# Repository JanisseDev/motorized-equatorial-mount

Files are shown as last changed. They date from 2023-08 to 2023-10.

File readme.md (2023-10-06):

# DIY Motorized Equatorial Mount

This project will guide you to create your own DIY Motorized Equatorial Mount controlled over wifi.

We will use a `28BYJ-48 stepper motor` coupled with a `1:42` reduction gear ratio, controlled by a `Raspberry Pico W`.
It'll be powered by `4xAA 1.2v Ni-MH rechargeable battery`.
> [!WARNING]
>_Do **not** use other battery than Ni-MH, since their voltage can be higher and damage your `Raspberry Pico W`._

<p align="center">
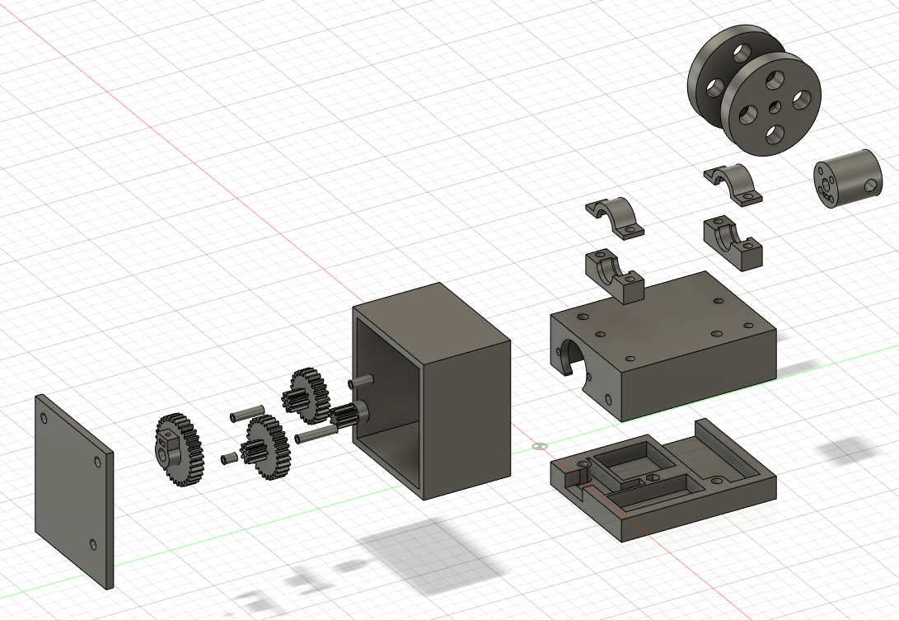
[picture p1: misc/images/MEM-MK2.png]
  
&nbsp;
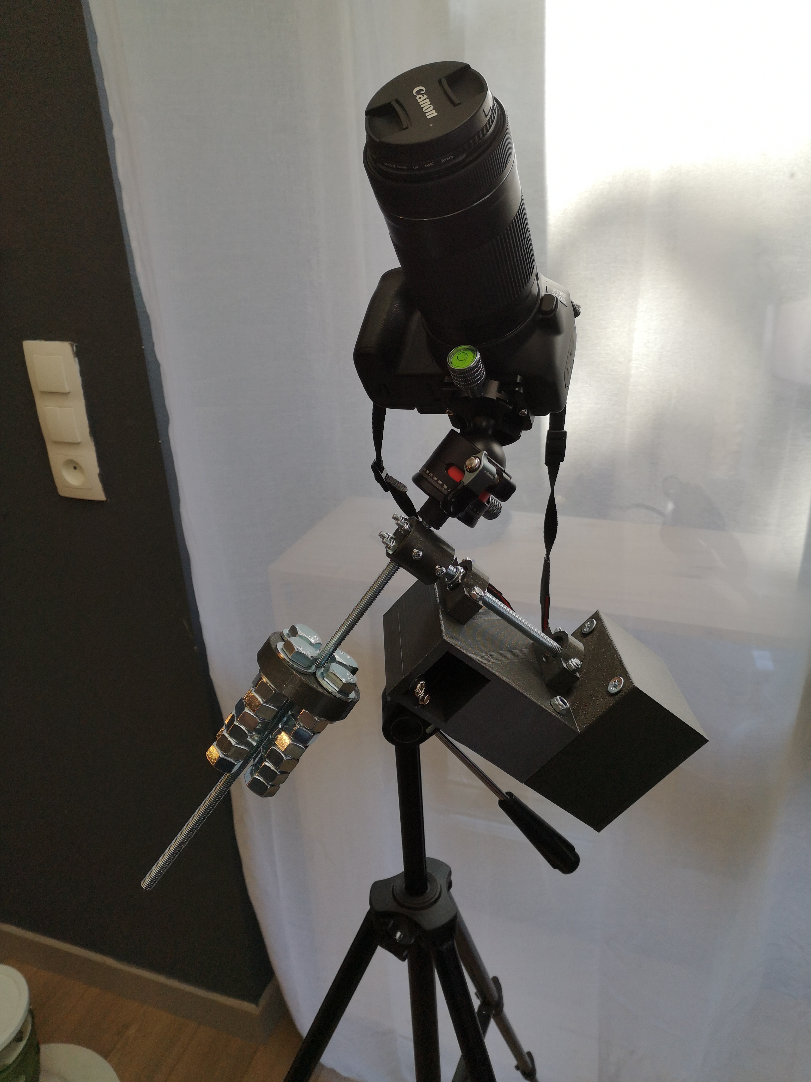
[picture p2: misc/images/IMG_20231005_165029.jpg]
  
</p>

## Item list
| Electronics | Case | Axis | Counterweight | Bearings |
| :---: | :---: | :---: | :---: | :---: |
| x1 Raspberry Pico W | x1 M6 bolt (80mm) | x1 M8 threaded Rod (500mm) | x1 M8 nut | x4 M5 bolt (30mm) |
| x1 28BYJ-48 stepper motor | x2 M6 bolt (70mm) | x2 M8 self-locking nut | x4 M12 screw (80mm) | x2 Skate bearing ABEC 7 |
| x1 ULN2003 driver board | x2 M6 bolt (50mm) | x4 M4 bolt (40mm) | x24 M12 nut | - |
| x1 4xAA case | x2 M4 bolt (20mm) | x2 M3 bolt (20mm) | - | - |
| Jumper wires | x1 M4 screw (40mm) | x1 M3 bolt (16mm) | - | - |
| - | x1 M4 wing nut | x2 nail (70mm x 3mm diameter) | - | - |

> [!NOTE]
>_This build requires some additional tools:_
> - _A metal saw to cut the M8 threaded Rod_
> - _A soldering iron to connect the power source to the Raspberry Pico W and the Motor driver board_

## Printing instructions
Print all the 3D files located in the [3dPrints](./misc/3dPrints/) folder.
All the files are already correctly oriented for printing, and are designed to use the smallest amount of supports as possible.
I printed these with an Ender-3 Pro, 0.4mm nozzle, layer height 0.2mm and with gyroid infill set to around 20% to 40%.
Some files needs to be printed multiple time, here is a list of pieces you should end up with:
| Count | Piece | Infill | Need supports |
| :---: | :---: | :---: | :---: |
| 1 | AxisMount-MEM-MK2 | 30% | Yes |
| 2 | BearingBottom-MEM-MK2 | 40% | No |
| 2 | BearingTop-MEM-MK2 | 40% | Yes |
| 2 | Counterweight-MEM-MK2 | 20% | No |
| 1 | Gear8-24-MEM-MK2 | 40% | No |
| 1 | Gear8-28-MEM-MK2 | 40% | No |
| 1 | Gear8-MEM-MK2 | 40% | No |
| 1 | Gear32-MEM-MK2 | 40% | No |
| 1 | GearSpacer8mm-MEM-MK2 | 40% | No |
| 1 | GearSpacer14mm-MEM-MK2 | 40% | No |
| 1 | GearSpacer20mm-MEM-MK2 | 40% | No |
| 1 | GearSpacer26mm-MEM-MK2 | 40% | No |
| 1 | GearCaseBottom-MEM-MK2 | 20% | No |
| 1 | GearCaseTop-MEM-MK2 | 20% | No |
| 1 | MainCaseBottom-MEM-MK2 | 20% | No |
| 1 | MainCaseTop-MEM-MK2 | 20% | Yes |

## Electrical diagram
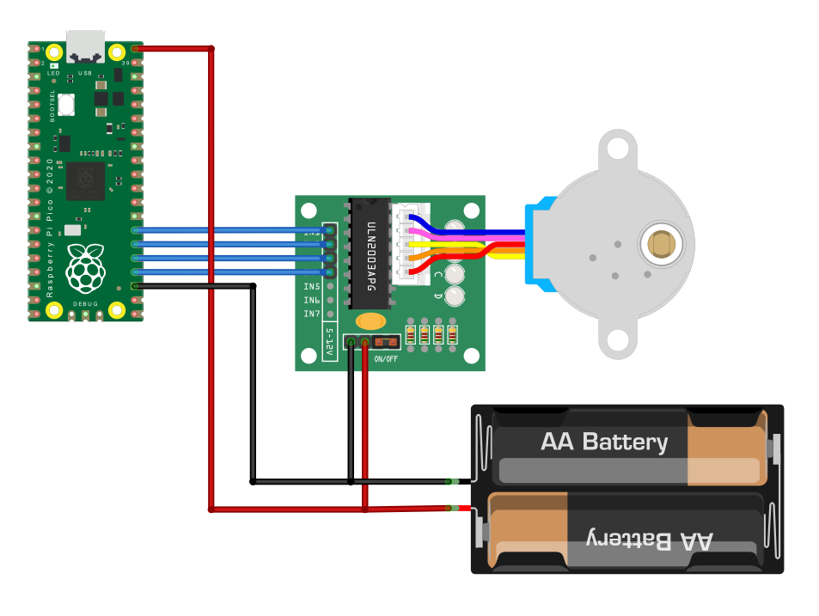
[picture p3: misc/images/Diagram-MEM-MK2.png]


## Assembly instructions
- Place the `Skate bearings` between `BearingTop` & `BearingBottom` pieces. Then mount them on the `MainCaseTop` with `x4 M5 bolt (30mm)`.
- Assemble the `Gear8` and the `motor` together.
- Place the `motor` inside the `GearCaseBottom`, put the `GearCaseBottom` on the side of `MainCaseTop` and screw them together with `x2 M4 bolt (20mm)`.
- Cut a 200mm piece from the `M8 threaded Rod`. We'll refer to it as the `main axis`. (Tip: You can easily cut a screw/rod without damaging it: screw some nuts near the spot you want to cut, clamp these nuts to a steady surface and cut your screw/rod)
- Put the `Gear32` at the very end of the `main axis` and secure it with a `x1 M3 bolt (16mm)`.
- Slide the `main axis` inside the bearings with the gear nearly inside the `GearCaseBottom` top. Secure it with `x2 M8 self-locking nut` by tightening the two nuts with a bearing between. (See [Gallery](#Gallery))
- Cut both ends of the `x2 nail (3mm diameter)` to a height of 60mm. These will serve as our intermediate gears' axes.
- Mount the `GearSpacer14mm`-`Gear8-24`-`GearSpacer20mm` on one of these axis, and put it inside the `GearCaseBottom`, in the furthest notch from the motor. (Tip: You can put some Blu-Tack inside the notch to help the axis standing while you assemble the whole thing)
- Repeat the process with the `GearSpacer26mm`-`Gear8-28`-`GearSpacer8mm`, in the nearest notch from the motor this time.
- Put the `GearCaseTop` on the `GearCaseBottom`, then secure it with `x2 M6 bolt (70mm)` and `x1 M6 bolt (80mm)`. (Make sure both intermediate gears axis are secured in their respective notch)
- Add `x4 M4 bolt (40mm)` to the `AxisMount`. (These are only here to secure the camera if the piece break)
- Mount the `AxisMount` on the `main axis` and secure it with `x1 M3 bolt (20mm)`.
- Cut a 300mm piece from the `M8 threaded Rod`. We'll refer to it as the `secondary axis`. (This axis will handle the camera and the counterweight)
- Mount the `secondary axis` on the `AxisMount` and secure it with `x1 M3 bolt (20mm)`.
- Put the `Raspberry Pico W` and the `ULN2003 driver board` inside the `MainCaseBottom`.
- Add `x1 M4 screw (40mm)` in the center hole. This will be used as a mounting screw on a tripod with the `x1 M4 wing nut`.
- Flash the `Raspberry Pico W` with [this binary](./misc/release/motorized_equatorial_mount.uf2).
- Connect all the electronics together (See the [electrical diagram](#electrical-diagram) above).
- Assemble the `MainCaseBottom` to the `MainCaseTop` with `x2 M6 bolt (50mm)`. (I highly suggest you to wrap the `4xAA case` wires around the screw)
- Put `x1 M8 nut` between the two `Counterweight` pieces and screw them together with `x4 M12 screw (80mm)` and `x24 M12 nut`. (You can put more or less nuts to customize your counterweight)
- You can now mount your camera on the `secondary axis` with an M8 to 1/4" adapter, for exemple, and screw the counterweight on the other side to balance it.

## User instructions
- Plug your 4xAA to the Motorized Equatorial Mount.
- Connect your phone to the wifi access point named `equatorial mount` (by default the password is `polar-star`). Open your browser and go to `192.168.4.1`
- You can now control the motor direction & speed from the web page. **The preset speed of 501ms between each motor step should be good to track stars if you use the same gear ratio & motor as mentioned in the Item list.**
- Unplug your 4xAA batteries to power down the system.
- Remove your camera and counterweight when not in use to prevent stress on the gears.

## Gallery
<p align="center">
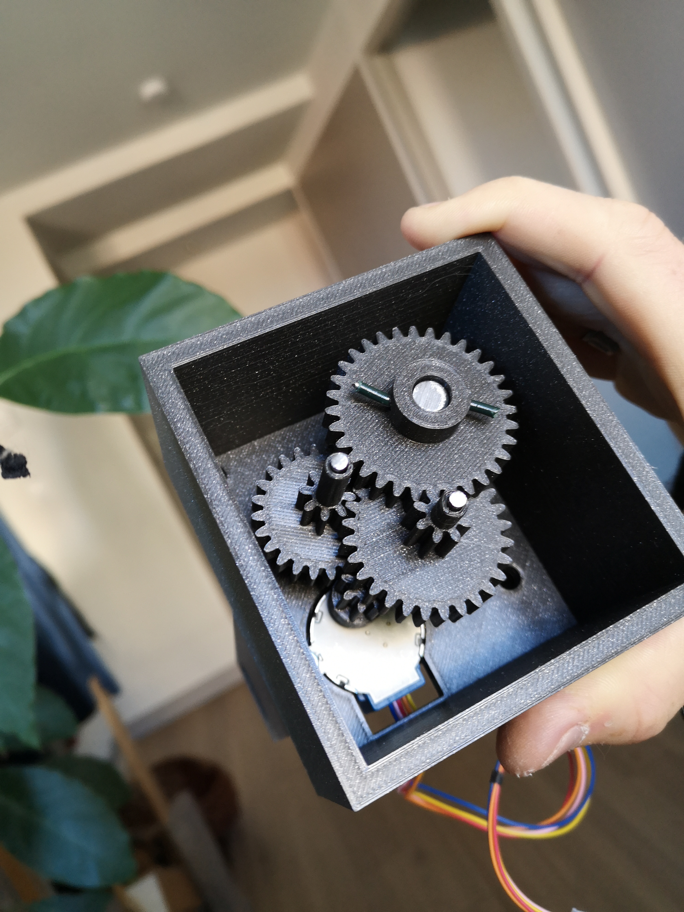
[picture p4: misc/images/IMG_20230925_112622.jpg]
  
&nbsp;
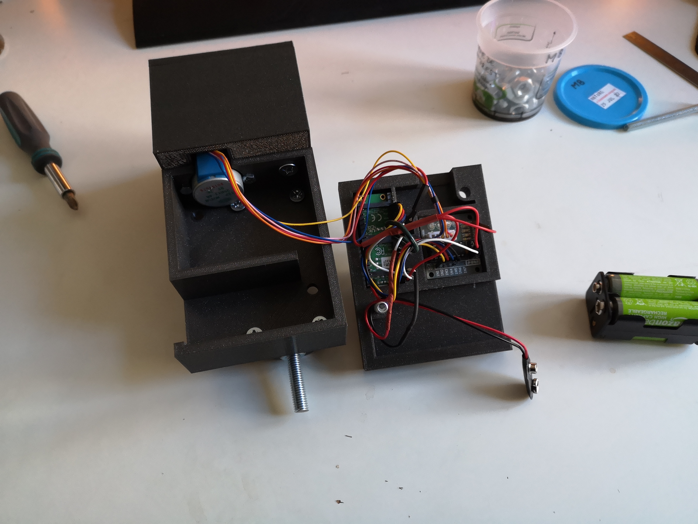
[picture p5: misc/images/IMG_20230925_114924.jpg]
  
</p>
<p align="center">
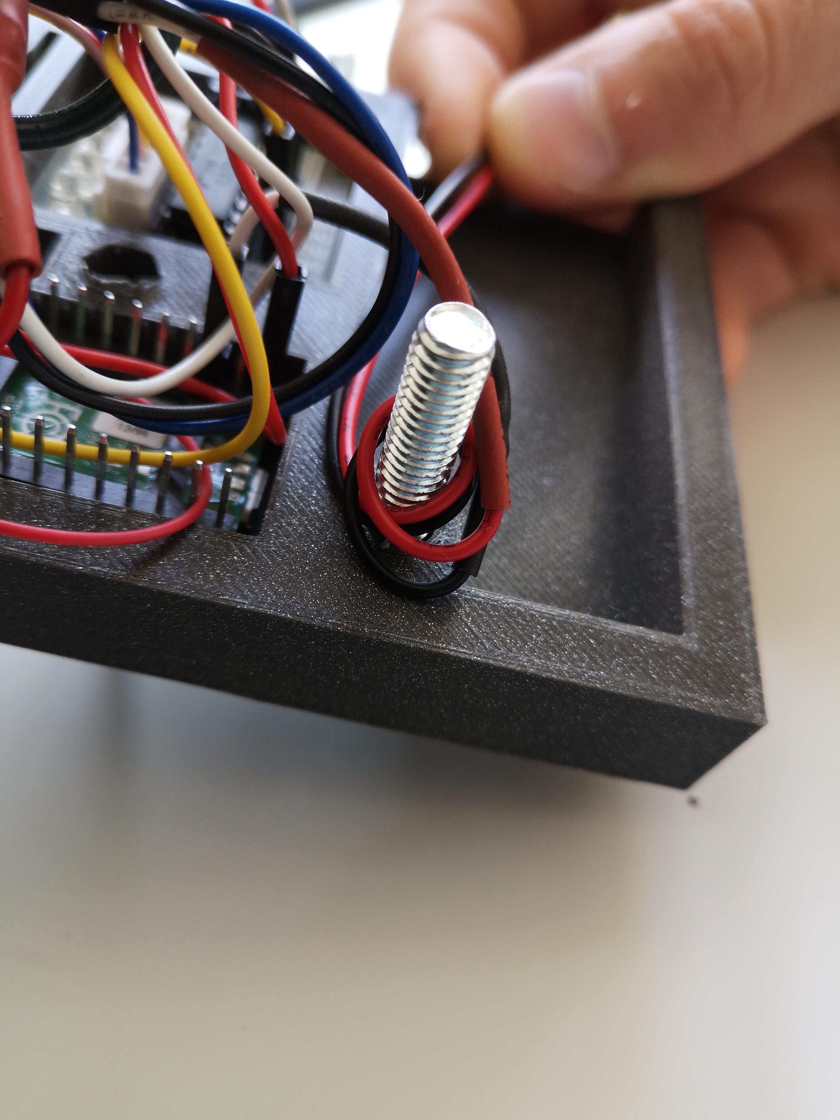
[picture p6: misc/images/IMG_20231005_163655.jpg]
  
&nbsp;
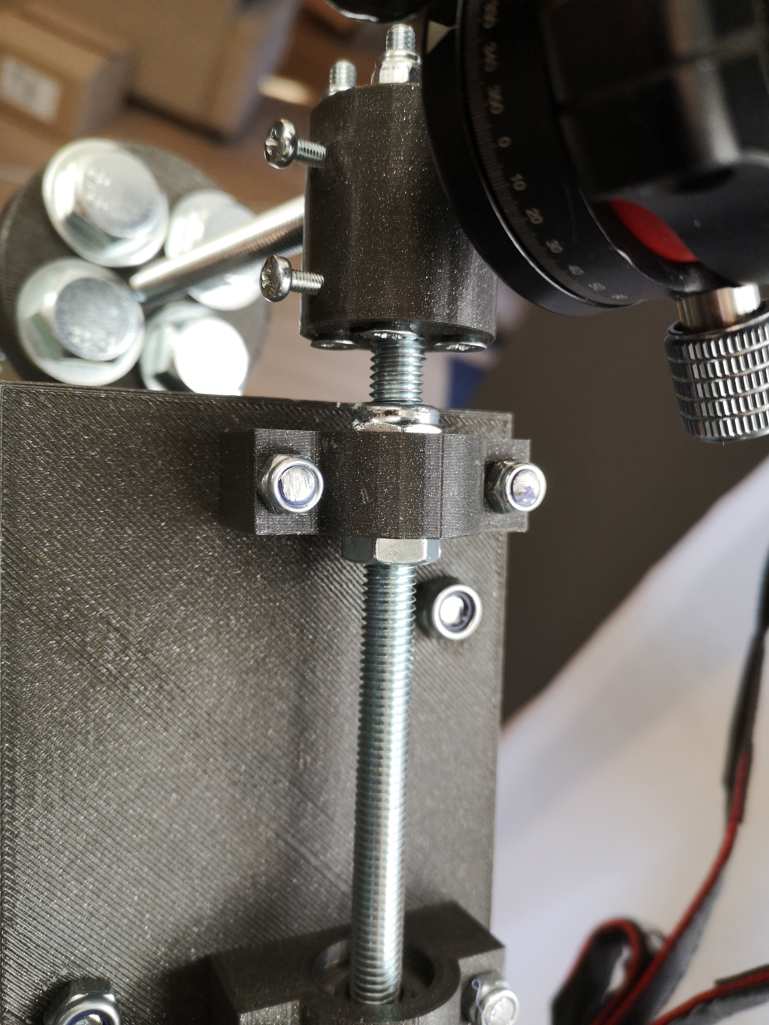
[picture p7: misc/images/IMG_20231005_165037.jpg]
  
</p>

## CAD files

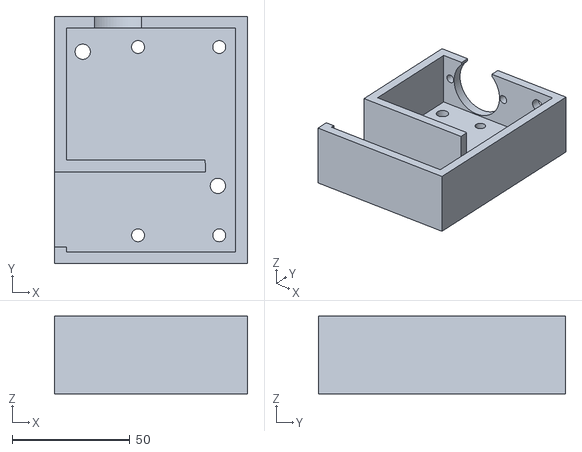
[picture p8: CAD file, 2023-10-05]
misc/3dPrints/MainCaseTop-MEM-MK2.stl
82.0 x 105.0 x 33.0

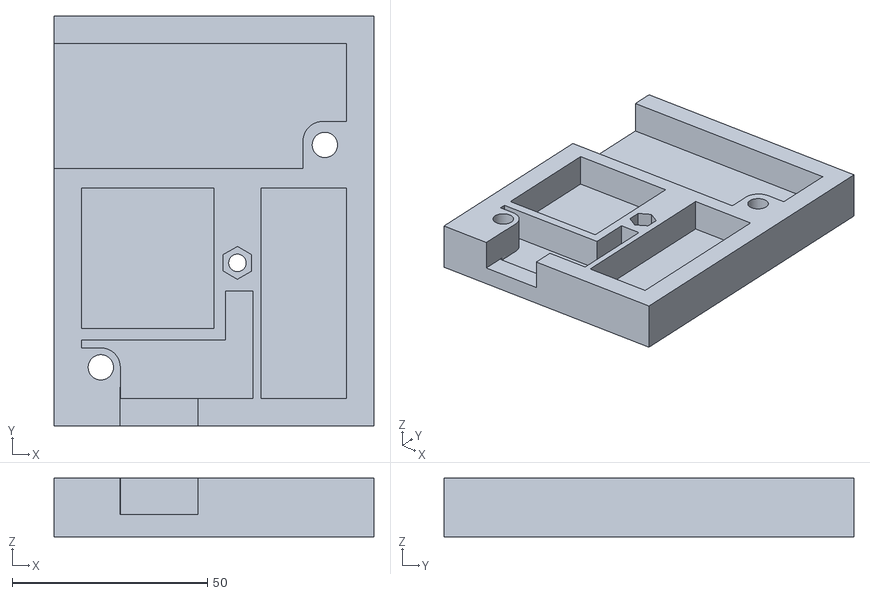
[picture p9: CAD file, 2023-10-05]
misc/3dPrints/MainCaseBottom-MEM-MK2.stl
82.0 x 105.0 x 15.0

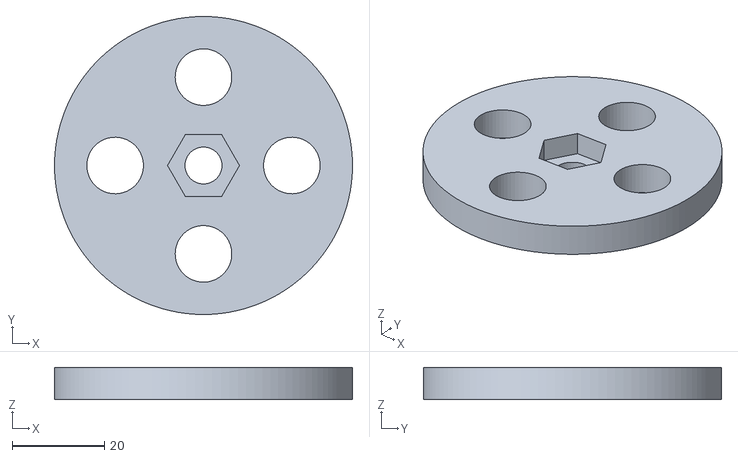
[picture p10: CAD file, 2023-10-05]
misc/3dPrints/Counterweight-MEM-MK2.stl
64.5 x 64.5 x 7.00

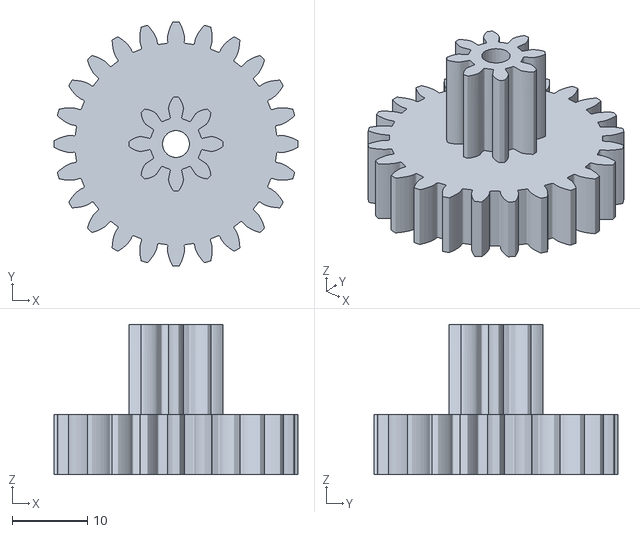
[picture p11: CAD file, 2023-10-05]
misc/3dPrints/Gear8-24-MEM-MK2.stl
32.5 x 32.5 x 20.0

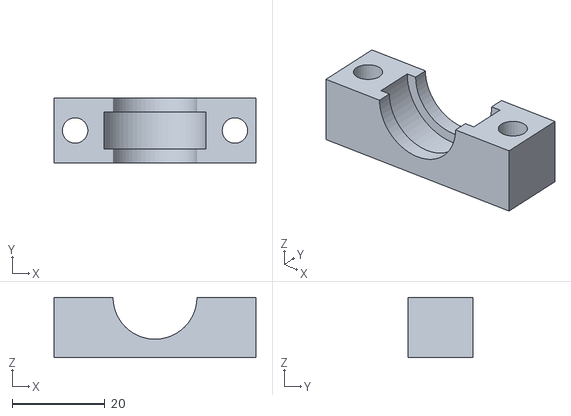
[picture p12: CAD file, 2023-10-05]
misc/3dPrints/BearingBottom-MEM-MK2.stl
43.6 x 14.0 x 13.0

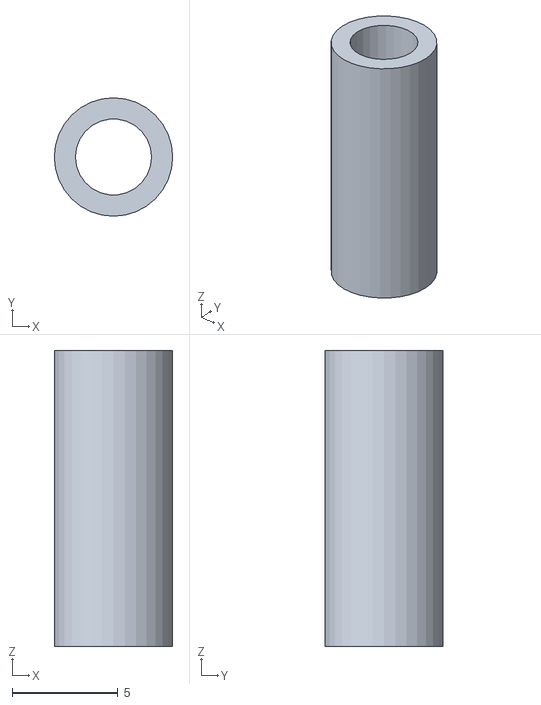
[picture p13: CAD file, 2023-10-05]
misc/3dPrints/GearSpacer14mm-MEM-MK2.stl
5.60 x 5.60 x 14.0

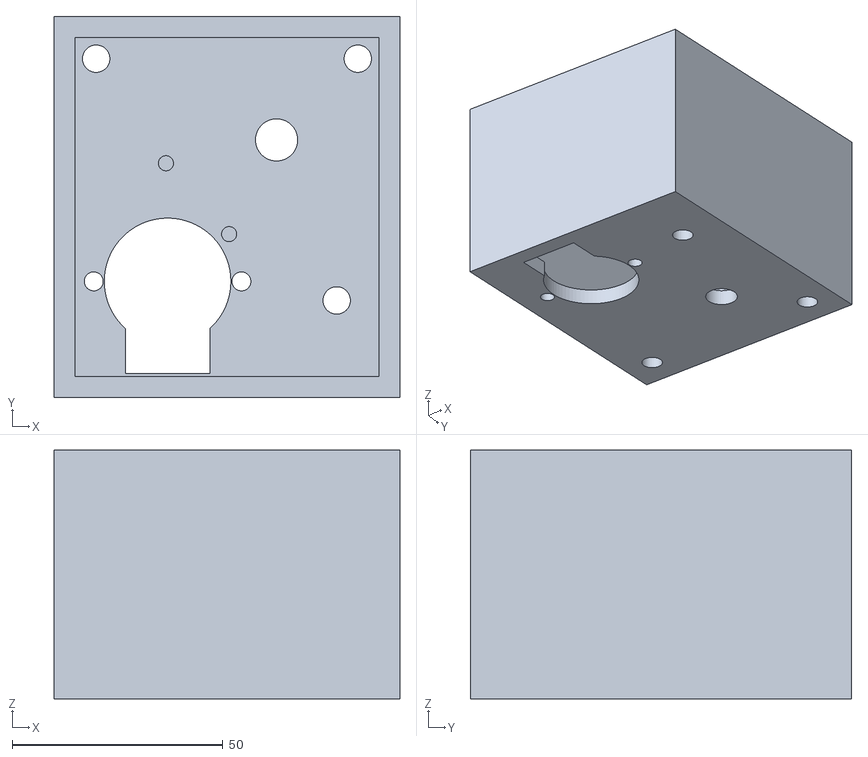
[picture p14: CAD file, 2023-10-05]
misc/3dPrints/GearCaseBottom-MEM-MK2.stl
82.0 x 90.3 x 59.0

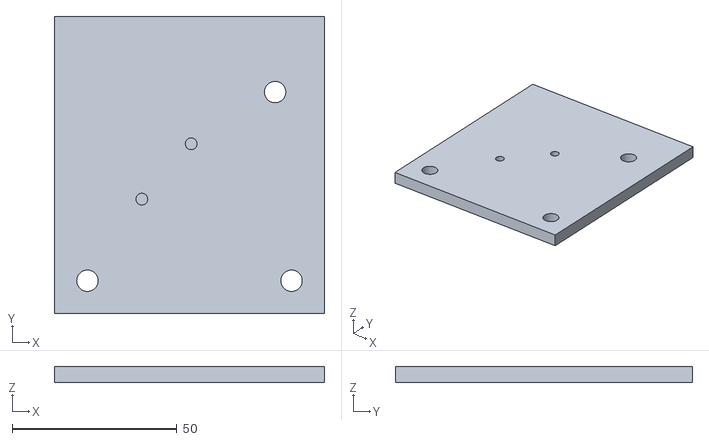
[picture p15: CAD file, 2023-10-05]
misc/3dPrints/GearCaseTop-MEM-MK2.stl
82.0 x 90.3 x 5.00

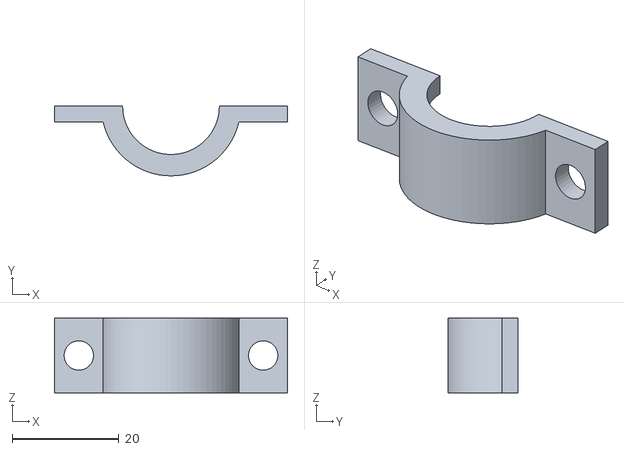
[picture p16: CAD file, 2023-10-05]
misc/3dPrints/BearingTop-MEM-MK2.stl
43.6 x 13.0 x 14.0

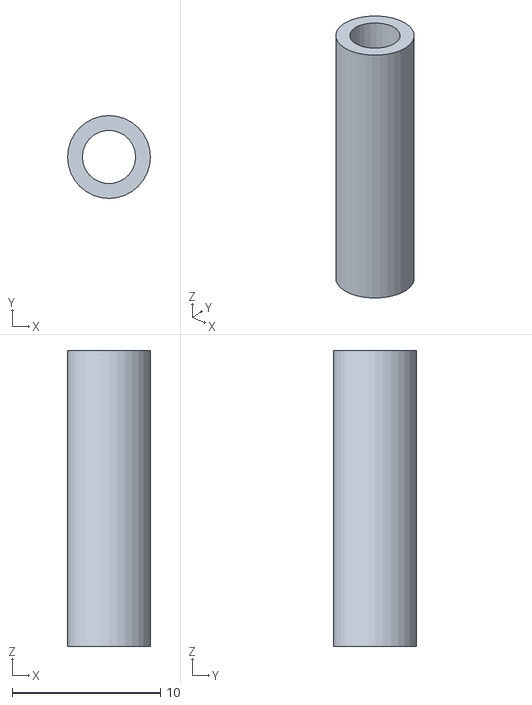
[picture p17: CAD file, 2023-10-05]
misc/3dPrints/GearSpacer20mm-MEM-MK2.stl
5.60 x 5.60 x 20.0

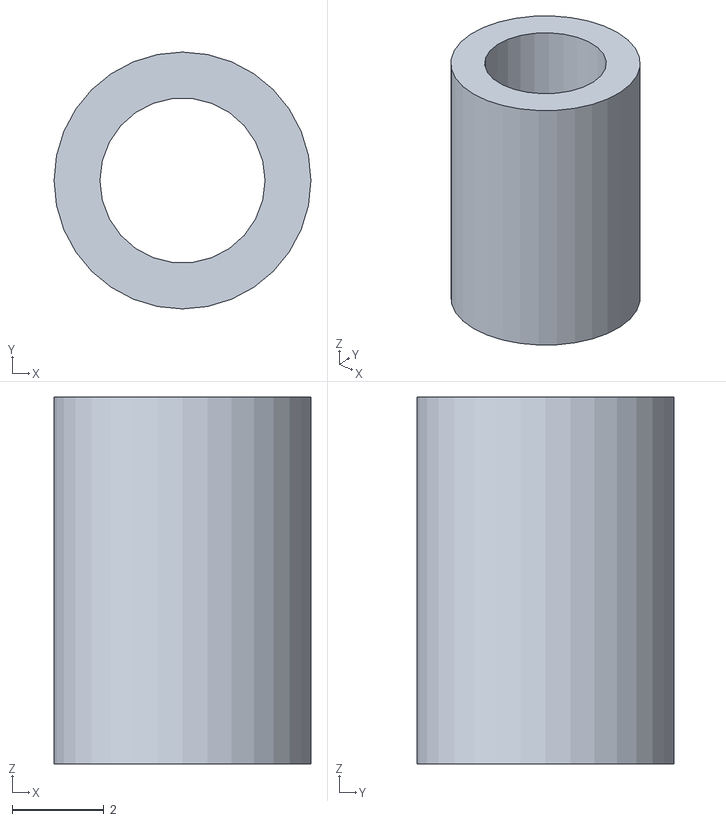
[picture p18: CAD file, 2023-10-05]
misc/3dPrints/GearSpacer8mm-MEM-MK2.stl
5.60 x 5.60 x 8.00

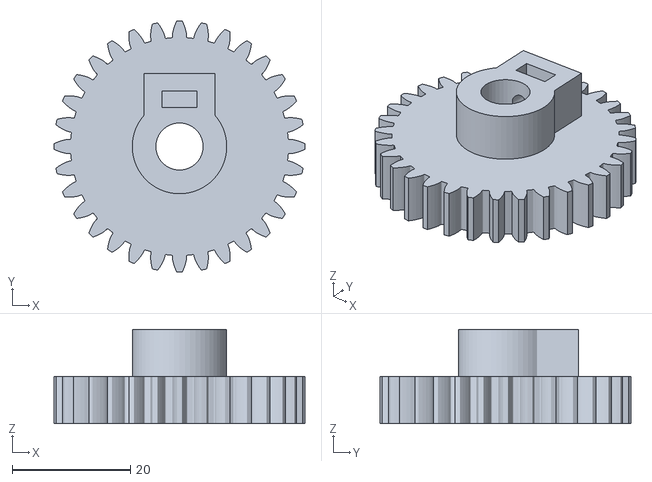
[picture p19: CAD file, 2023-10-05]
misc/3dPrints/Gear32-MEM-MK2.stl
42.5 x 42.5 x 16.0

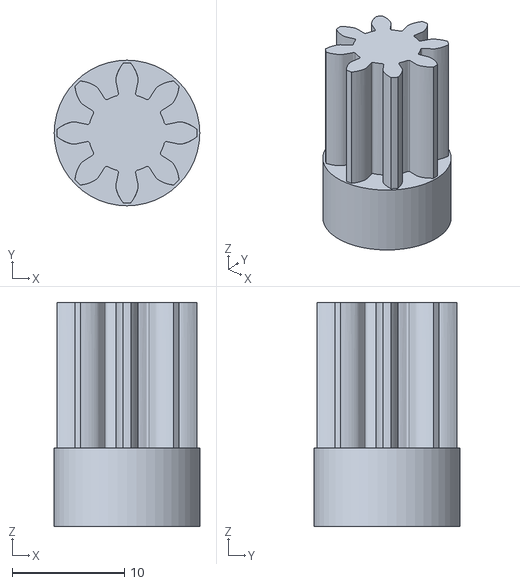
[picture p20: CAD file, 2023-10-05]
misc/3dPrints/Gear8-MEM-MK2.stl
13.0 x 13.0 x 20.0

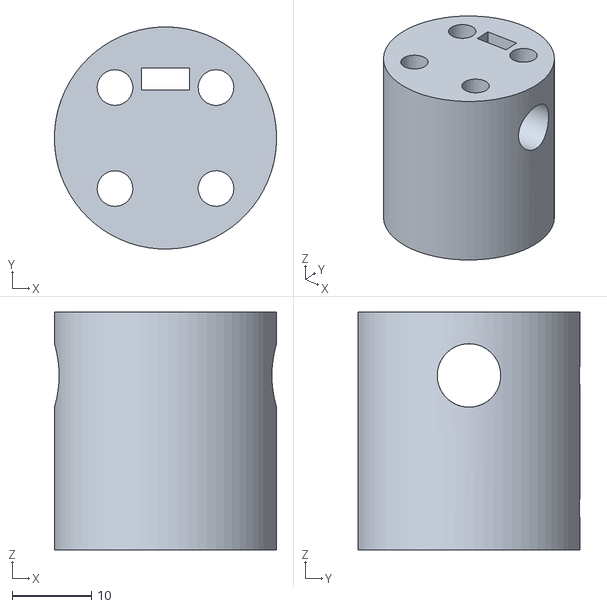
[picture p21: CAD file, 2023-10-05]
misc/3dPrints/AxisMount-MEM-MK2.stl
28.0 x 28.0 x 30.0

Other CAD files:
misc/3dPrints/GearSpacer26mm-MEM-MK2.stl
misc/3dPrints/Gear8-28-MEM-MK2.stl

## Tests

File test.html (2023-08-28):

# Motorized equatorial mount

LED

ON OFF

Speed

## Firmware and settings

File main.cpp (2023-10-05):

/**
 * Copyright (c) 2022 Raspberry Pi (Trading) Ltd.
 *
 * SPDX-License-Identifier: BSD-3-Clause
 */

// This template is based on the "access_point" exemple from https://github.com/raspberrypi/pico-examples/tree/master/pico_w/wifi/access_point

#include "controlVariables.h"
#include "server.h"

// Declare ControlVariables
volatile bool blinking = false;
volatile uint32_t blinkSpeed = 100;
volatile MotorMode motorMode = MotorMode::Stopped;
volatile uint32_t motorSpeed = 501;

// Init Motor constants
const uint stepCount = 8;
int steps[8][4] = {{1, 0, 0, 0}, {1, 1, 0, 0}, {0, 1, 0, 0}, {0, 1, 1, 0}, {0, 0, 1, 0}, {0, 0, 1, 1}, {0, 0, 0, 1}, {1, 0, 0, 1}};
const uint MOTOR_PIN_1 = 18;
const uint MOTOR_PIN_2 = 19;
const uint MOTOR_PIN_3 = 20;
const uint MOTOR_PIN_4 = 21;

int nextStep(int currentStep, bool backward) {
    if (backward) {
        if (currentStep <= 0) {
            return stepCount-1;
        } else {
            return currentStep-1;
        }
        return currentStep-1;
    } else {
        return (currentStep+1)%stepCount;
    }
}

int main() {
    // Init
    stdio_init_all();
    if (cyw43_arch_init()) {
        DEBUG_printf("failed to initialise\n");
        return 1;
    }
    
    // You can setup your access point name & password here
    int serverInitResult = serverInit("equatorial mount", "polar-star");
    if(serverInitResult != 0) {
        return serverInitResult;
    }

    // New way to light the onboard led
    cyw43_gpio_set(&cyw43_state, 0, true);


    // Init Motor GPIO
    gpio_init(MOTOR_PIN_1);
    gpio_init(MOTOR_PIN_2);
    gpio_init(MOTOR_PIN_3);
    gpio_init(MOTOR_PIN_4);
    gpio_set_dir(MOTOR_PIN_1, GPIO_OUT);
    gpio_set_dir(MOTOR_PIN_2, GPIO_OUT);
    gpio_set_dir(MOTOR_PIN_3, GPIO_OUT);
    gpio_set_dir(MOTOR_PIN_4, GPIO_OUT);

    int currentStep = 0;
    while(!state->complete) {
        // Do your usual pico stuff here
        if (motorMode != MotorMode::Stopped) {
            gpio_put(MOTOR_PIN_1, steps[currentStep][0]);
            gpio_put(MOTOR_PIN_2, steps[currentStep][1]);
            gpio_put(MOTOR_PIN_3, steps[currentStep][2]);
            gpio_put(MOTOR_PIN_4, steps[currentStep][3]);
            currentStep = nextStep(currentStep, motorMode == MotorMode::Backward);
            sleep_ms(motorSpeed);
        } else {
            sleep_ms(100);
        }
    }

    serverDeinit();
    return 0;
}

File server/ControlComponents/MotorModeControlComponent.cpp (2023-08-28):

#include <string>
#include <vector>

#include "server.h"
#include "controlVariables.h"

class MotorModeControlComponent {
private:
    static std::string generate_content(MotorMode currentMode) {
        const std::string selectedClass = "class='selected'";
        return "\
<div class='cell'>\
    <p>Motor mode</p>\
    <div class='switch'>\
        <a "+((motorMode==MotorMode::Backward)?selectedClass:"")+" href='?motorMode=-1'>Backward</a>\
        <a "+((motorMode==MotorMode::Stopped)?selectedClass:"")+" href='?motorMode=0'>Stopped</a>\
        <a "+((motorMode==MotorMode::Forward)?selectedClass:"")+" href='?motorMode=1'>Forward</a>\
    </div>\
</div>";
    }

public:
    static void check_params(const char *params)
    {
        int value;
        int matchCount = sscanf(params, "motorMode=%d", &value);
        if (matchCount == 1) {
            motorMode = (MotorMode)value;
        }
    }

    static std::string html_content()
    {
        // Generate result
        return generate_content(motorMode);
    }
};

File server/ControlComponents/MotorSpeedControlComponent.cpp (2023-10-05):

#include <string>
#include <vector>

#include "server.h"
#include "controlVariables.h"

class MotorSpeedControlComponent {
private:
    static std::string generate_content(uint32_t currentValue) {
        return "\
<div class='cell'>\
    <p>Motor speed</p>\
    <form>\
        <input type='number' name='motorSpeed' style='width: 100px;' value='"+std::to_string(currentValue)+"' min='8' max='10000'/>\
        <input type='submit' value='Send'/>\
    </form>\
</div>";
    }

public:
    static void check_params(const char *params)
    {
        uint32_t value;
        int matchCount = sscanf(params, "motorSpeed=%d", &value);
        if (matchCount == 1) {
            motorSpeed = value;
        }
    }

    static std::string html_content()
    {
        // Generate result
        return generate_content(motorSpeed);
    }
};

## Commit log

2023-08-22 Add 'access_point' template project from pico-examples
2023-08-25 Create LED control component
2023-08-25 Add MotorSpeedControlComponent
    Note: /!\ blinkInterval variable is not shared across cores /!\
2023-08-26 Fix blinkInterval sharing between cores
    [MotorSpeedControlComponent.cpp, main.cpp]
2023-08-26 Add comment about current ControlVariables implementation
2023-08-28 Remove fixed buffer size limitation
    [webpage.cpp]
2023-08-28 Add motor control support
2023-10-05 Upload 3D models & Maths note
    [AxisMount-MEM-MK2.stl, BearingBottom-MEM-MK2.stl, BearingTop-MEM-MK2.stl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]
2023-10-05 Reorganize folders + Add photos
    [AxisMount-MEM-MK2.stl, BearingBottom-MEM-MK2.stl, BearingTop-MEM-MK2.stl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]
